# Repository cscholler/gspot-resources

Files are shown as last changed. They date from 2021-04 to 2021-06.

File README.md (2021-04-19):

# gspot-resources
All the documentation to keep room 214 running in the event that something breaks

Motor controller is dual H-bridge XY-160D
Motors are Bosch Seat Motors sold by AndyMark as [am-3493](https://wpilib.screenstepslive.com/s/4485/m/63630/l/679357-bosch-seat-motor)
Power Supply is 12v 30a regulated switching [power supply](https://www.amazon.com/gp/product/B06VWV5YCH/ref=ppx_od_dt_b_asin_title_s00?ie=UTF8&psc=1)

Guide rails are 8020 10 series, [Part No. 1010](https://8020.net/1010.html)
Winch cable is Home Depot [1/16th Galvanized Steel Wire Rope](https://www.homedepot.com/p/Everbilt-1-16-in-x-250-ft-Galvanized-Vinyl-Coated-Steel-Wire-Rope-806370/203958870)

Winch drum is comprised of three laser cut 1/4in acrylic circles, two angled 3D printed PLA pieces held together with three brass binding screws, McMaster [93813A342](https://www.mcmaster.com/93813A342/) - If these come loose use a bit of locktight

[Limit switches](https://www.amazon.com/dp/B07ZVJD1GC?psc=1&ref=ppx_yo2_dt_b_product_details) are held on with 3D printed mounts and 10/32 socket head bolts with T-nuts.

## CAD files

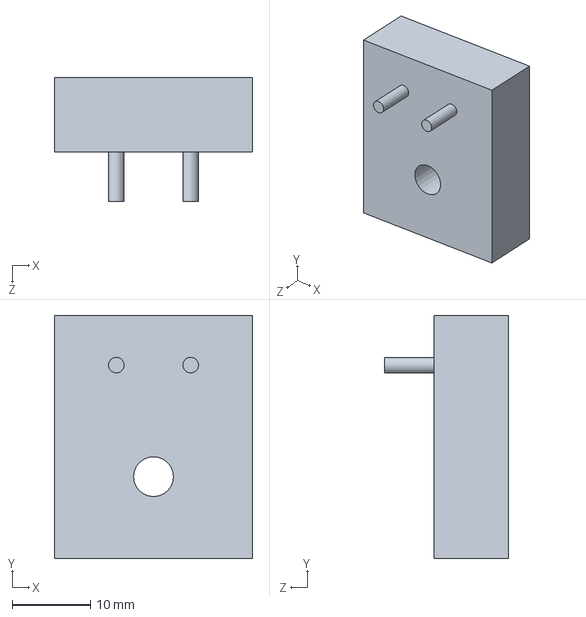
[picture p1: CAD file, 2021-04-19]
Parts/limitSwitchMount1.SLDPRT
25.4 x 31.1 x 15.9 mm

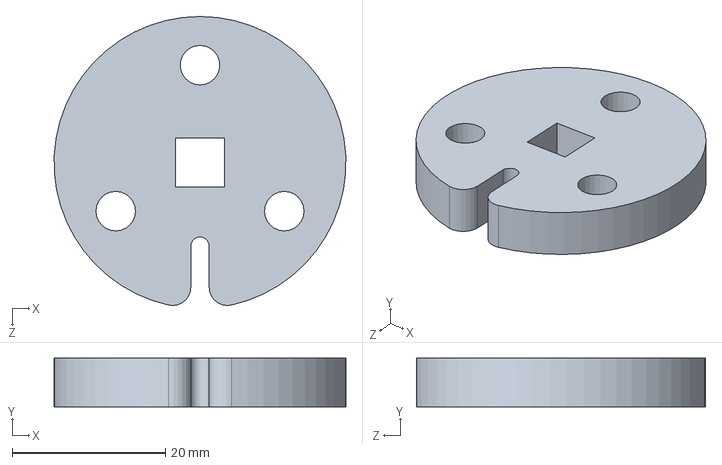
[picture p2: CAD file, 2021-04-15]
Parts/slot pulley.SLDPRT
38.1 x 6.35 x 37.7 mm

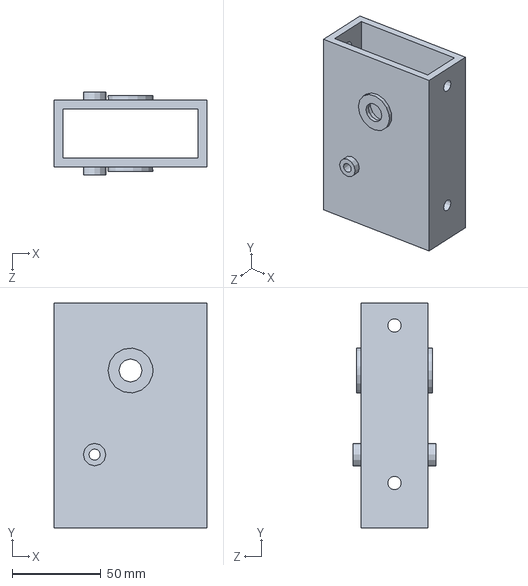
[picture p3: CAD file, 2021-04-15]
Parts/Motor mount.SLDPRT
86.4 x 127.0 x 46.9 mm

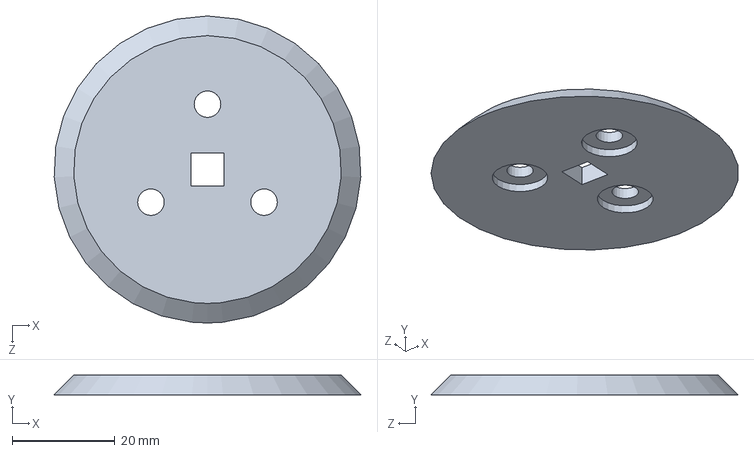
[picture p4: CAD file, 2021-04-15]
Parts/pulley guide.SLDPRT
59.6 x 3.81 x 59.7 mm

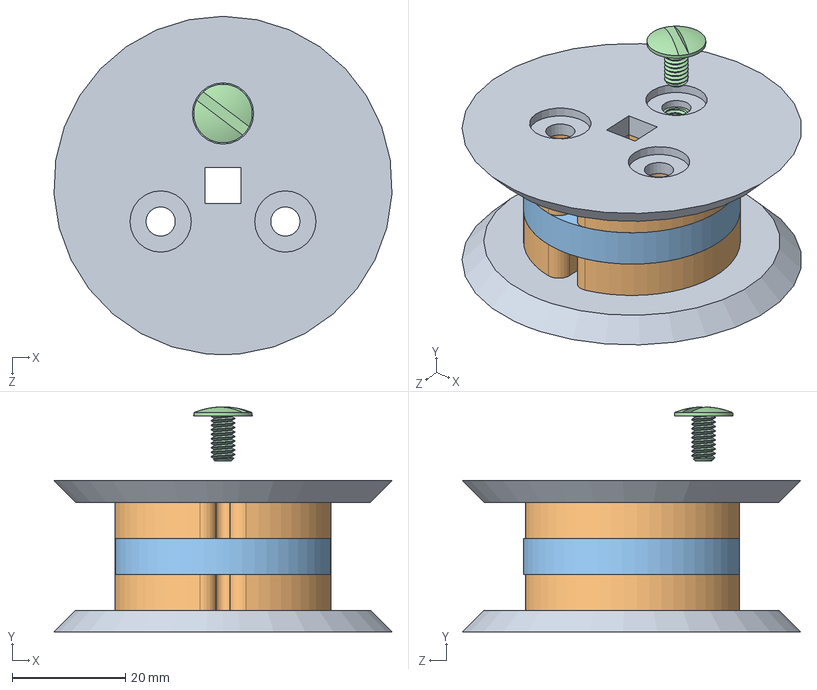
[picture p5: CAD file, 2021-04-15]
Parts/screw compound pulley.SLDASM
59.6 x 39.7 x 59.7 mm
pulley guide x 2
slot pulley x 2
hole pulley
93813A342_BRASS LOW-PROFILE BINDING POST

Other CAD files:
Parts/hole pulley.SLDPRT
Parts/motor mount print 11.10.STL
Parts/hole pulley.DXF
Parts/limitSwitchMount1.STL
Parts/slot pulley.DXF

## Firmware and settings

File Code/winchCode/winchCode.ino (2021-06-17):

#include "Button.h"
#include "Motor.h"
#include "Lock.h"
#include "Actuator.h"

#include <arduino-timer.h>

enum State_enum {CALIBRATE, WAIT, MOVE, HOLD, ADJUST};
enum Switch_enum {MIN, MAX};

// DoorHead & WindowHead
#define H_IN1 4
#define H_IN2 2
#define WH_ENA 5
#define DH_ENA 3

// DoorFoot & WindowFoot
#define F_IN1 12
#define F_IN2 13
#define WF_ENA 10
#define DF_ENA 11

#define UP_PIN 6  // Yellow
#define DN_PIN 7  // Blue

// Yellow
#define WH_TOP A3
#define WH_BOTTOM A2
// Green
#define DH_TOP 9
#define DH_BOTTOM 8
// Red
#define WF_TOP A5
#define WF_BOTTOM A4
// White
#define DF_TOP A1
#define DF_BOTTOM A0

#define NORMALLY_CLOSED true
#define NORMALLY_OPEN false

// Create objects to be used later
auto timer = timer_create_default();

Motor wh_motor(H_IN1, H_IN2, WH_ENA);
Motor dh_motor(H_IN1, H_IN2, DH_ENA);
Motor wf_motor(F_IN1, F_IN2, WF_ENA);
Motor df_motor(F_IN1, F_IN2, DF_ENA);

Button upButton(UP_PIN, NORMALLY_CLOSED);
Button dnButton(DN_PIN, NORMALLY_CLOSED);

Button wh_button_min(WH_BOTTOM, NORMALLY_CLOSED);
Button wh_button_max(WH_TOP, NORMALLY_CLOSED);
Button dh_button_min(DH_BOTTOM, NORMALLY_CLOSED);
Button dh_button_max(DH_TOP, NORMALLY_CLOSED);
Button wf_button_min(WF_BOTTOM, NORMALLY_CLOSED);
Button wf_button_max(WF_TOP, NORMALLY_CLOSED);
Button df_button_min(DF_BOTTOM, NORMALLY_CLOSED);
Button df_button_max(DF_TOP, NORMALLY_CLOSED);

Actuator wh_actuator(wh_button_max, wh_button_min, wh_motor);
Actuator dh_actuator(dh_button_max, dh_button_min, dh_motor);
Actuator wf_actuator(wf_button_max, wf_button_min, wf_motor);
Actuator df_actuator(df_button_max, df_button_min, df_motor);

bool atTop;
bool atBottom;

void setup() {
  Serial.begin(9600);
  atTop = false;
  atBottom = false;
}

void loop() {
  timer.tick();
  //    wh_motor.moveAtSpeed(1);
  //    dh_motor.moveAtSpeed(1);
  //    wf_motor.moveAtSpeed(1);
  //    df_motor.moveAtSpeed(1);
  // If only the 'up button' is pressed then begin actions to move upwards
  if (upButton.isPressed() && !dnButton.isPressed()) {
    Serial.println("up");
    // If the bed is currently resting on the booth then run calibration before lifting
    if (atBottom) {
      // To calibrate lift corner until it's just above the booth then wait until all corners have done the same
      Serial.println("At bottom");
      int actuatorCounter = 0;
      if (wh_actuator.calibrate(MIN) == WAIT) actuatorCounter++;
      if (dh_actuator.calibrate(MIN) == WAIT) actuatorCounter++;
      if (wf_actuator.calibrate(MIN) == WAIT) actuatorCounter++;
      if (df_actuator.calibrate(MIN) == WAIT) actuatorCounter++;

      // Once calibration is complete and all corners are just above resting on the booth set 'atBottom' to false and continue
      if (actuatorCounter >= 4) {
        Serial.println("Calibration complete");
        atBottom = false;
      }
      // If the bed is not at the top of its travel distance then pull each corner upwards until they get there
    } else if (!atTop) {
      // Lift each corner until it's reached the upper limit switch and wait until all corners have done the same
      Serial.println("Moving up");
      int actuatorCounter = 0;
      if (wh_actuator.moveToMax() == WAIT) actuatorCounter++;
      if (dh_actuator.moveToMax() == WAIT) actuatorCounter++;
      if (wf_actuator.moveToMax() == WAIT) actuatorCounter++;
      if (df_actuator.moveToMax() == WAIT) actuatorCounter++;

      // Check that all corners have reached their upper limit switch, if they have then set 'atTop' to true
      if (actuatorCounter >= 4) {
        Serial.println("Reached top");
        atTop = true;
      }
      // If the bed is pressing all of the upper limit switches then set all motors to hold at top
    } else if (atTop) {
      Serial.println("At top");
      wh_actuator.hold();
      dh_actuator.hold();
      wf_actuator.hold();
      df_actuator.hold();
    }

    // If any of the upper limit switches become unpressed then change 'atTop' back to false
    if (!wh_button_max.isPressed() || !dh_button_max.isPressed() || !wf_button_max.isPressed() || !df_button_max.isPressed()) {
      atTop = false;
    }

    // If only the 'down button' is pressed and the 'lock' is not engaged then begin actions to move downwards
  } else if (!upButton.isPressed() && dnButton.isPressed()) {
    Serial.println("down");
    // If the bed is not currently resting on the booth then move all corners down until it is
    if (!atBottom) {
      // Move all corners down until they are pressed the lower limit switch then wait until all corners have done the same
      Serial.println("Not at bottom");
      int actuatorCounter = 0;
      if (wh_actuator.moveToMin() == WAIT) actuatorCounter++;
      if (dh_actuator.moveToMin() == WAIT) actuatorCounter++;
      if (wf_actuator.moveToMin() == WAIT) actuatorCounter++;
      if (df_actuator.moveToMin() == WAIT) actuatorCounter++;

      // If all lower limit switches are pressed then set 'atBottom' to true and drive all motors for 0.5 sec to release tention
      if (actuatorCounter >= 4 ) {
        Serial.print("Reached bottom");

        wh_motor.down();
        dh_motor.down();
        wf_motor.down();
        df_motor.down();

        timer.every(1, [] {
          Serial.println("Hi");
          return NULL;
        });

        timer.in(500, [] {
          atBottom = true;
          Serial.println("--------------------------");
          return NULL;
        });

      }
      // If bed is resting on the booth then set all motors to hold
    } else {
      Serial.print("At bottom");
      wh_actuator.hold();
      dh_actuator.hold();
      wf_actuator.hold();
      df_actuator.hold();
    }

    atTop = false;

    // If the above conditions were not met then set all motors to hold
  } else {
    Serial.println("hold");
    wh_motor.hold();
    dh_motor.hold();
    wf_motor.hold();
    df_motor.hold();
  }
//  delay(10);
}

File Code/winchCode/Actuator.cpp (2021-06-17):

#include "Actuator.h"

enum State_enum {CALIBRATE, WAIT, MOVE, HOLD, ADJUST};
enum Switch_enum {MIN, MAX};

Actuator::Actuator() {}
Actuator::Actuator(Button maxSwitch, Button minSwitch, Motor actuatorMotor) {
  this->maxSwitch = maxSwitch;
  this->minSwitch = minSwitch;
  this->motor = actuatorMotor;
  this->state = WAIT;
}

void Actuator::setActuator(Button maxSwitch, Button minSwitch, Motor actuatorMotor) {
  this->maxSwitch = maxSwitch;
  this->minSwitch = minSwitch;
  this->motor = actuatorMotor;
  this->state = WAIT;
}

uint8_t Actuator::getState() {
  return state;
}

void Actuator::setState(uint8_t newState) {
  this->state = newState;
}

uint8_t Actuator::calibrate(uint8_t calibrationSwitchEnum) {
  state = CALIBRATE;
  Button calibrationSwitch = (calibrationSwitchEnum == MIN) ? minSwitch : maxSwitch;
  switch (state) {
    case CALIBRATE:
      if (calibrationSwitch.isPressed()) {
        calibrationSwitchEnum == MIN ? motor.up() : motor.down();
        break;
      }
      else state = WAIT;

    case WAIT:
      motor.moveAtSpeed(1);
      if (calibrationSwitch.isPressed()) state = CALIBRATE;

      break;
  }
  return state;
}

uint8_t Actuator::moveToMax() {
  state = MOVE;
  switch (state) {
    case MOVE:
      if (!maxSwitch.isPressed()) {
        Serial.println("State: MOVE");
        motor.up();
        break;
      }
      else {
        state = WAIT;
      }

    case WAIT:
    Serial.println("State: WAIT");
      motor.moveAtSpeed(1);
      break;
  }
  return state;
}

uint8_t Actuator::moveToMin() {
  state = MOVE;
  switch (state) {
    case MOVE:
      if (!minSwitch.isPressed()) {
        motor.down();
        break;
      }
      else {
        state = WAIT;
      }

    case WAIT:
      motor.moveAtSpeed(-1);
      break;
  }
  return state;
}

void Actuator::hold() {
  motor.hold();
}

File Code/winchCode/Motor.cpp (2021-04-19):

#include "Motor.h"

#define defaultSpeed 255

Motor::Motor() {}

Motor::Motor(byte IN1, byte IN2, byte ENA) {
  this->IN1 = IN1;
  this->IN2 = IN2;
  this->ENA = ENA;
  init();
}

void Motor::setMotor(byte IN1, byte IN2, byte ENA) {
  this->IN1 = IN1;
  this->IN2 = IN2;
  this->ENA = ENA;
  init();
}

void Motor::init() {
  pinMode(IN1, OUTPUT);
  pinMode(IN2, OUTPUT);
  pinMode(ENA, OUTPUT);
}

void Motor::up() {
  digitalWrite(IN1, HIGH);
  digitalWrite(IN2, LOW);
  analogWrite(ENA, defaultSpeed);
}

void Motor::down() {
  digitalWrite(IN1, LOW);
  digitalWrite(IN2, HIGH);
  analogWrite(ENA, defaultSpeed);
}

void Motor::idle() {
  digitalWrite(IN1, HIGH);
  digitalWrite(IN2, HIGH);
}

void Motor::hold() {
  digitalWrite(IN1, LOW);
  digitalWrite(IN2, LOW);
}

void Motor::moveAtSpeed(int moveSpeed) {
  if (moveSpeed >= 0) {
    digitalWrite(IN1, HIGH);
    digitalWrite(IN2, LOW);
    analogWrite(ENA, moveSpeed);
  } else if (moveSpeed < 0) {
    digitalWrite(IN1, LOW);
    digitalWrite(IN2, HIGH);
    analogWrite(ENA, abs(moveSpeed));
  }
}

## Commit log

2021-04-15 added solidworks parts
    [Motor mount.SLDPRT, hole pulley.DXF, hole pulley.SLDPRT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]
2021-04-19 Added limit switch mount CADs
    [limitSwitchMount1.SLDPRT, limitSwitchMount1.STL]
2021-06-17 removed lock made delay timer
